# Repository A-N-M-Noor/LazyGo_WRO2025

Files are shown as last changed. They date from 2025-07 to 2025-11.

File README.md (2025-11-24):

<div align="center">
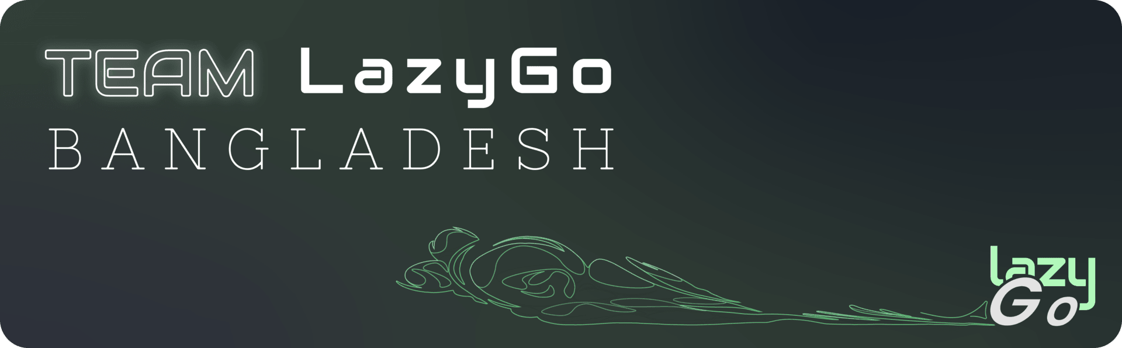
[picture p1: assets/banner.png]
  
</div>
  <strong>Team LazyGo</strong> is a robotics team from <strong>Bangladesh</strong>. Originally formed in 2022, LazyGo won <strong>3rd place</strong> at the Future Engineers category of the World Robot Olympiad International Round. Now the team returns again with three experienced international participants.
<br><br>

We named our robot **LazyBot**, which is built for the **Future Engineers** category in the **World Robot Olympiad 2025**. This year, we are trying to bring some interesting changes from the typical way a robot is built for this category. Definitely check out [Odometry Calculation](#odometry), [Disparity Extender Algorithm](#avoidance-using-lidar), and [LiDAR Based Tower Detection](#obstacle-round) algorithms.

This repository contains all the files, codes, models, photos and everything about our team and the robot.

Visit our team socials:





## Table of Contents

- [`Team Introduction`](#team-introduction)
- [`Mission Overview for WRO Future Engineers Rounds`](#mission-overview-for-wro-future-engineers-rounds)
- [`Repository`](#repository)
- [`Key Features`](#key-features)
- [`Components and Hardware`](#components-and-hardware)
- [`Algorithm`](#algorithm)
- [`Mobility Management`](#mobility-management)
- [`Power and Sense Management`](#power-and-sense-management)

---
## Team Introduction
<div>
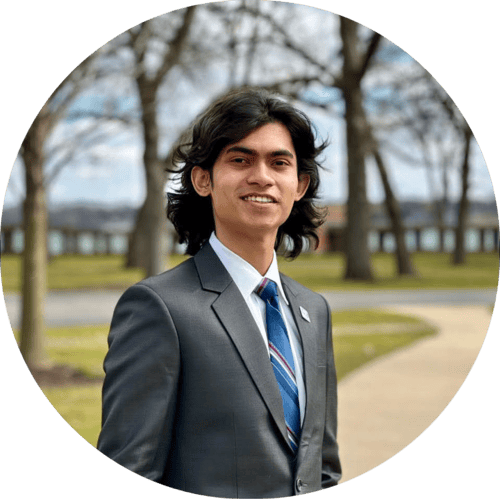
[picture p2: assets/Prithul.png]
  <br>
  <strong>Iqbal Samin Prithul</strong><br>
  Embedded Electronics<br>
  WRO 2022 International 3rd Place (Future Engineers Category)<br>
  <a href="mailto:prithul0218@gmail.com">prithul0218@gmail.com</a>
</div><br>

---
<div>
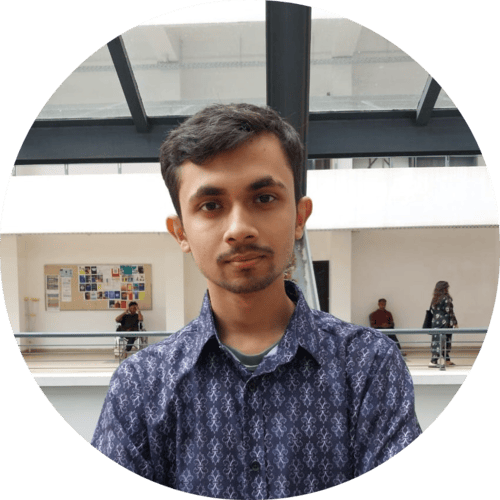
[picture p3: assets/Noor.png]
  <br>
  <div align="right">
  <strong>A.N.M Noor</strong><br>
  Software and ROS<br>
  WRO 2023 International Participant (Future Engineers Category)<br>
  <a href="mailto:noornoorrohan15@gmail.com">noornoorrohan15@gmail.com</a></div>
</div><br>

---
<div>
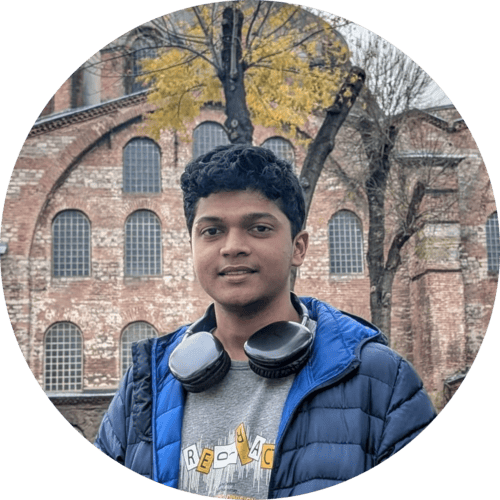
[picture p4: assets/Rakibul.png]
  <br>
  <strong>Rakibul Islam</strong><br>
  Hardware and CAD design<br>
  WRO 2024 International Participant (Future Engineers Category)<br>
  <a href="mailto:rakibul.rir06@gmail.com">rakibul.rir06@gmail.com</a>
</div><br>

---

---

## Mission Overview for WRO Future Engineers Rounds

<table>
  <tr>
    <td width="50%" valign="top" align="center"><h3>🏁 Round 1: Lap Completion</h3></td>
    <td width="50%" valign="top" align="center"><h3>🏆 Round 2: Lap Completion with Obstacle Avoidance and Parking</h3></td>
  </tr>
  <tr>
    <td width="50%" valign="top" align="left">
      <p>In <strong>Round 1</strong>, the robot must autonomously complete <strong>three laps</strong> on a pre-defined track. The goal of this round is for the bot to demonstrate stable navigation and precise lap tracking without any obstacle avoidance requirements.</p>
      <ul>
        <li><strong>Objective</strong>: Complete three laps on the track within the allotted time.</li>
        <li><strong>Key Tasks</strong>: Accurate path-following, speed control, and lap counting.</li>
      </ul>
      <div align="center" valign="bottom">
        <br><br><br><br>
        Round 1 WRO Track
      </div>
    </td>
    <td width="50%" valign="top" align="left">
      <p>In <strong>Round 2</strong>, the bot must complete <strong>three laps</strong> while avoiding green and red obstacles:</p>
      <ul>
        <li><strong>Green Obstacles</strong>: The bot should move <strong>left</strong> to avoid.</li>
        <li><strong>Red Obstacles</strong>: The bot should move <strong>right</strong> to avoid.</li>
      </ul>
      <p>After completing the laps, the bot must accurately park within a designated zone.</p>
      <ul>
        <li><strong>Objective</strong>: Complete three laps, avoid obstacles, and park in the designated area.</li>
        <li><strong>Tasks</strong>: Obstacle detection, color-based avoidance, and precision parking.</li>
      </ul>
      <div align="center">
        Round 2 WRO Track
      </div>
    </td>
  </tr>
</table>

---
>[!IMPORTANT]
>**Important: WRO Future Engineers Rulebook**
>* **Thorough Reading:** Ensure that you thoroughly read the **WRO Future Engineers 2025 Rulebook** to understand all rules and guidelines.
>* **Official Link:** Access the rulebook here: [🔗 WRO Future Engineers 2025 Rulebook](https://wro-association.org/wp-content/uploads/WRO-2025-Future-Engineers-Self-Driving-Cars-General-Rules.pdf).

---
## Repository

This repository includes all files, designs, and code for **LazyBot**, our WRO 2025 robot.

### File Structure

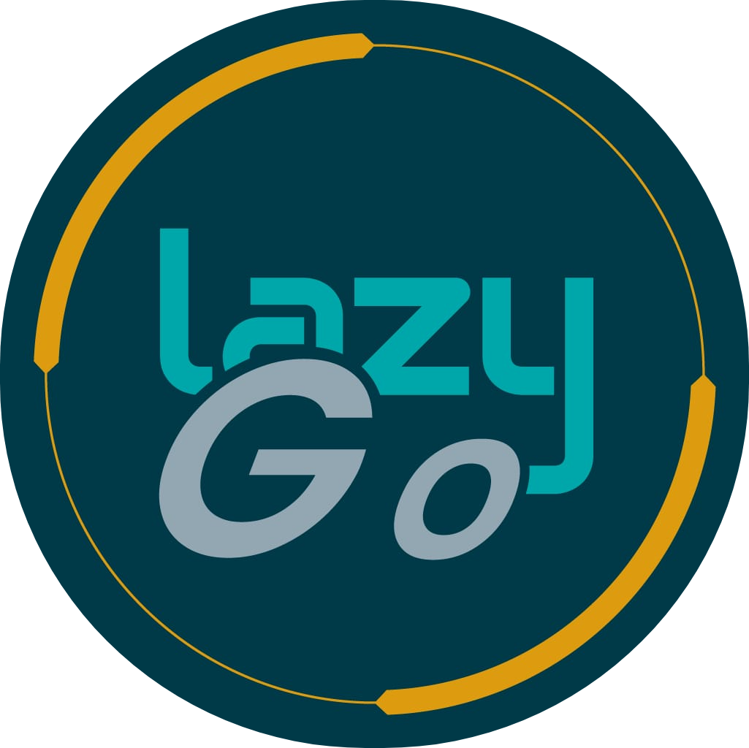
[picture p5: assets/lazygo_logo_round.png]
LazyBot

Here’s a breakdown of the project folders:

- **[`assets`](./assets/)**: Contains all the images used in the README files of this repository.
- **[`instructions`](./instructions/)**: Contains all the instructions on how to setup and use the package.
- **[`models`](./models/)**: Contains 3D models and CAD designs of the robot.
- **[`src`](./src/)**: Source code for the robot's programming. This contains the ROS2 packages.
- **[`t-photos`](./t-photos/)**: Technical images of the robot build.
- **[`v-photos`](./v-photos/)**: Visual photos for aesthetics and showcasing.
- **[`video`](./video/)**: Performance and demo videos of LazyBot.

---
---

## Key Features

- **`Hybrid LEGO & 3D Printed Design`**: Using LEGO parts proved to be very helpful based on the previous experience of our members. That, along with 3D printed parts made it possible to harness LEGO's precision and the flexibility of 3D printing.
- **`Advanced Sensor Suite`**: LazyBot is equipped with a LiDAR (to perfectly sense the surroundings), encoder motor (to precisely calculate the position), IMU (to calculate realtime orientation).
- **`Use of Robot Operating System`**: We used ROS2 to control the robot. We took this decision because Robot Operating System allows to make a project very modular and provide a lot of useful tools for simulation and visualization.
- **`Real-Time Odometry Calculation`**: This is one of the major feature of our robot. Using the onboard IMU sensor and the value from the motor's encoder, the robot calculates the exact realtime position of the robot.
- **`Efficient Debugging`**: We've added an OLED display to the MCU of the robot which helps to debug the issues on the MCU side. And ROS2 provides a lot of debugging tools that helps us debug any issues happening on the Pi side.

---
---

## Components and Hardware

Our bot is equipped with various components that support its autonomous functionality. The table below summarizes each module with a concise role and mounting approach:

<table>
  <thead>
    <tr>
      <th>Image</th>
      <th>Component</th>
      <th>Price</th>
      <th>Role / Function</th>
      <th>Mounting</th>
    </tr>
  </thead>
  <tbody>
    <tr>
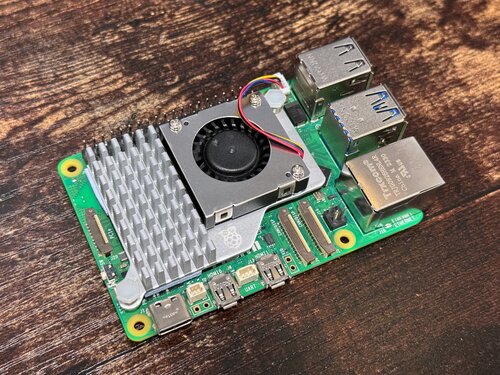
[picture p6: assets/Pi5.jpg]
Raspberry Pi 5
      <td></td>
      <td><a href="https://www.aliexpress.com/item/1005008153885728.html">Raspberry Pi 5</a></td>
      <td>$100.00</td>
      <td>High‑level processing (ROS2, vision, LiDAR integration). 8GB RAM for parallel tasks.</td>
      <td>3D printed middle chassis plate + 4× M2.5 standoffs & screws.</td>
    </tr>
    <tr>
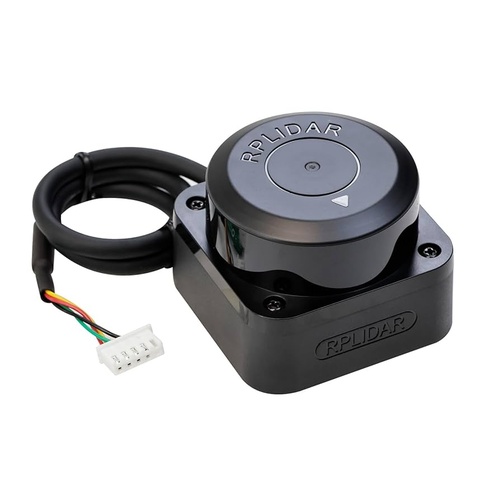
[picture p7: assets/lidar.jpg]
RPLidar C1
      <td></td>
      <td><a href="https://www.aliexpress.com/item/1005007915572042.html">RPLidar C1</a></td>
      <td>$67.87</td>
      <td>360° environment scan for obstacle mapping & tower shape profiling.</td>
      <td>Top cover LiDAR mount, 4× M2.5 screws. Resting on middle layer tray for support.</td>
    </tr>
    <tr>
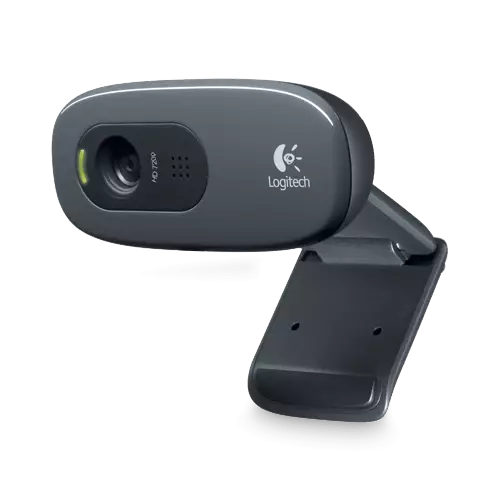
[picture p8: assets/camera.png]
C270
      <td></td>
      <td><a href="https://www.aliexpress.com/item/1005005033359539.html">Logitech C270 Camera</a></td>
      <td>$24.76</td>
      <td>Color tower detection (masking & confirmation).</td>
      <td>Mounted on 3D printed pan servo mount with single screws for angle adjustment.</td>
    </tr>
    <tr>
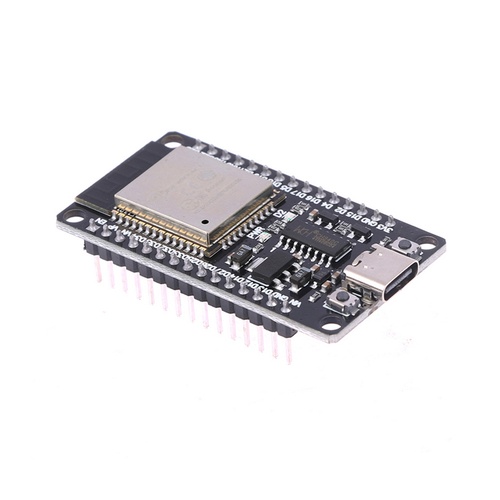
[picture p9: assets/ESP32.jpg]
ESP32
      <td></td>
      <td><a href="https://www.aliexpress.com/item/1005006826620736.html">ESP32 Microcontroller</a></td>
      <td>$7.38</td>
      <td>Real‑time motor, encoder, IMU, servo & OLED interface; low‑level comms.</td>
      <td>Soldered to custom secondary PCB under top cover.</td>
    </tr>
    <tr>
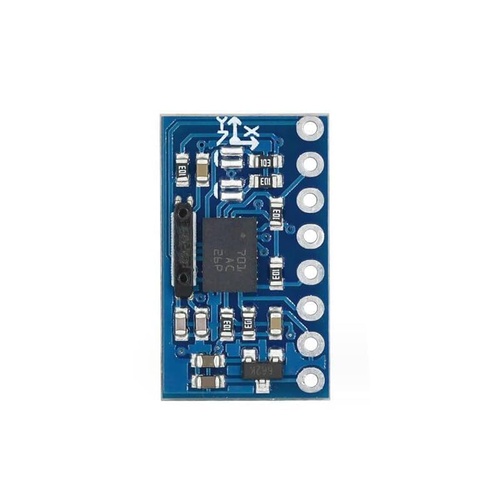
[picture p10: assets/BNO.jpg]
BNO055
      <td></td>
      <td><a href="https://www.aliexpress.com/item/1005009534591471.html">BNO055 9‑Axis IMU</a></td>
      <td>$22.28</td>
      <td>Orientation & fused heading for odometry; low drift angle source.</td>
      <td>Center (slightly left) of PCB for vibration isolation; header pins + foam tape as spacer for mild vibration dampening.</td>
    </tr>
    <tr>
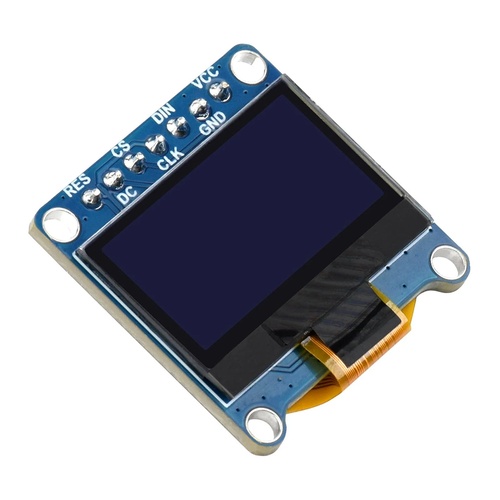
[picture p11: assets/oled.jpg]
OLED
      <td></td>
      <td><a href="https://www.aliexpress.com/item/1005008934254841.html">1.3" OLED (I2C)</a></td>
      <td>$5.83</td>
      <td>Live status: sensor readouts, battery warnings, debug info.</td>
      <td>Vertical raised header on PCB rear edge + friction with top cover.</td>
    </tr>
    <tr>
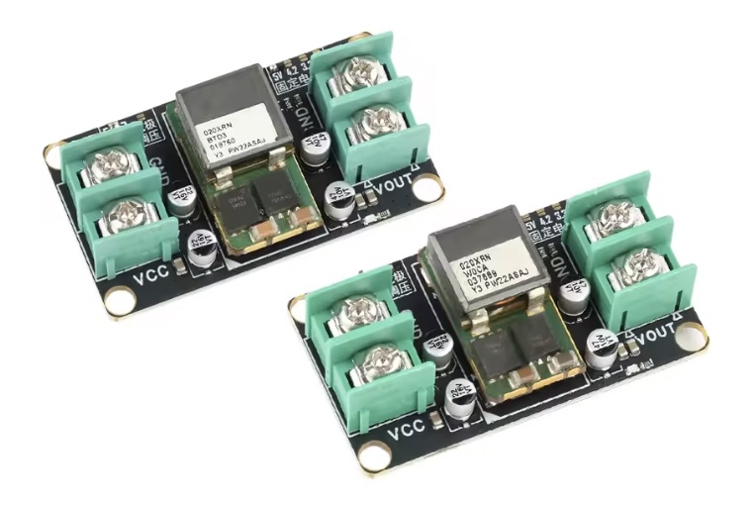
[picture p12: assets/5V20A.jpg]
5V 20A Buck
      <td></td>
      <td><a href="https://www.aliexpress.com/item/1005008785628197.html">5V 20A Buck Converter</a></td>
      <td>$6.21</td>
      <td>Primary regulated 5V rail for Pi (headroom for peaks).</td>
      <td>Middle chassis plate with double sided tape.</td>
    </tr>
    <tr>
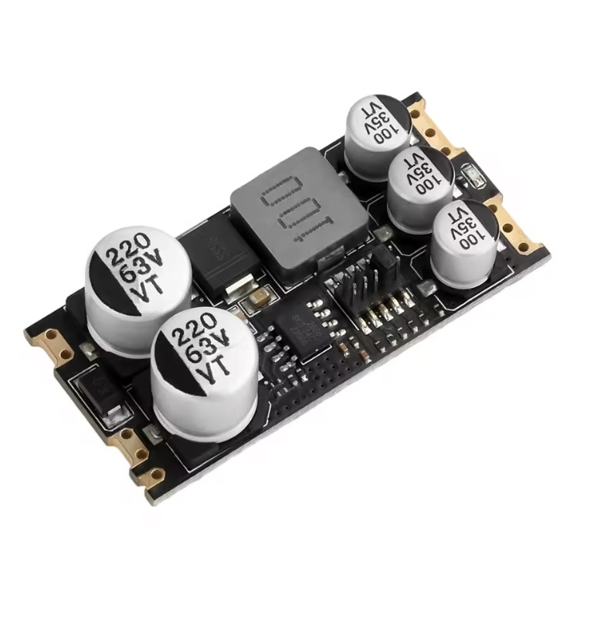
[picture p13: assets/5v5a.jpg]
5V 5A Buck
      <td></td>
      <td><a href="https://www.aliexpress.com/item/1005008477697348.html">5V 5A Buck (SCT2650)</a></td>
      <td>$3.99</td>
      <td>Secondary regulated supply for noise generating components (Servo, peripherals).</td>
      <td>Bottom of PCB (to save space).</td>
    </tr>
    <tr>
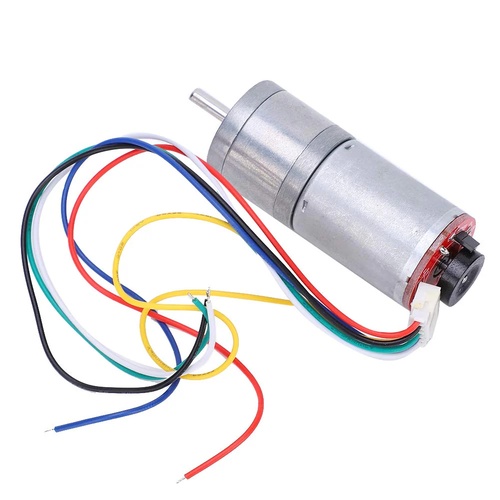
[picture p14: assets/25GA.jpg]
25GA Motor
      <td></td>
      <td><a href="https://www.aliexpress.com/item/1005008766288833.html">25GA Gear Motors + Encoder</a></td>
      <td>$9.65</td>
      <td>Drivetrain torque + linear displacement feedback for odometry.</td>
      <td>Captured in printed motor housings; 2× M3 screws.</td>
    </tr>
    <tr>
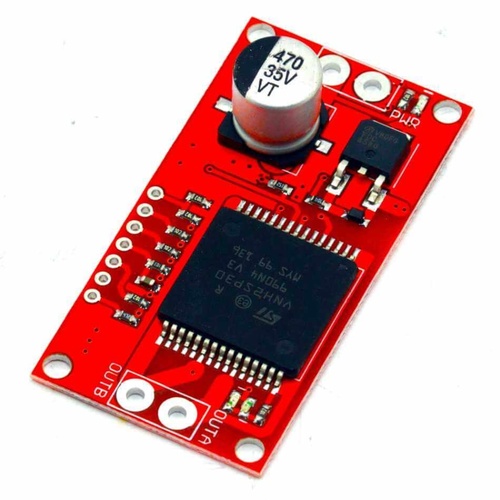
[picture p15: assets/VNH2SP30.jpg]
Motor Driver
      <td></td>
      <td><a href="https://www.aliexpress.com/item/1005006213746966.html">VNH2SP30 Motor Driver</a></td>
      <td>$18</td>
      <td>High‑current brushed DC control (PWM + direction + protection).</td>
      <td>Screwed to the bottom of the second/middle layer.</td>
    </tr>
    <tr>
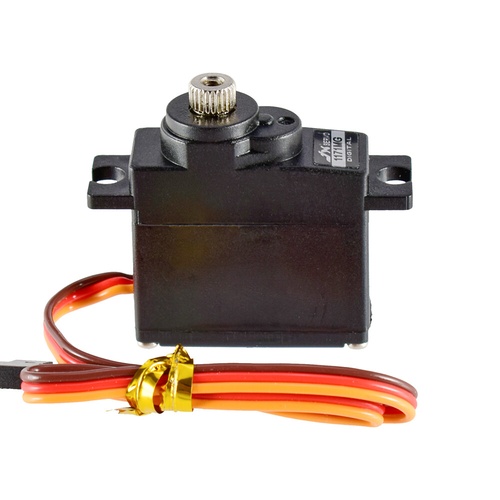
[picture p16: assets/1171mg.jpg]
Servo
      <td></td>
      <td><a href="https://www.aliexpress.com/item/1005002533411942.html">PS1171MG Servo</a></td>
      <td>$16.00</td>
      <td>Steering actuation & camera pan positioning.</td>
      <td>3D printed steering bracket/3D printed LiDAR bracket with integrated servo hole. 2× self‑tapping screws each.</td>
    </tr>
    <tr>
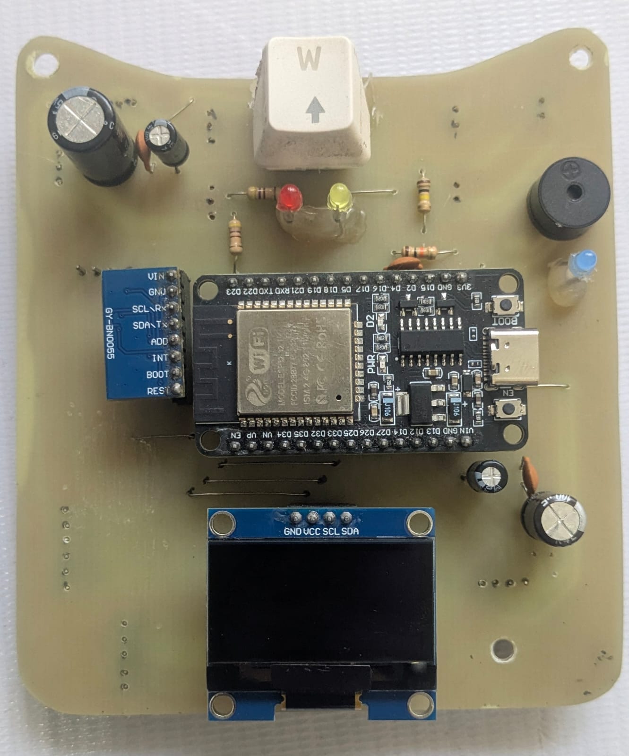
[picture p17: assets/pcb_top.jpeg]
Secondary PCB
      <td></td>
      <td>Custom Secondary PCB</td>
      <td>N/A</td>
      <td>Integration hub: ESP32, IMU, OLED, some power distribution, headers and lots of capacitors.</td>
      <td>Four M3 standoffs to chassis mid‑deck and top cover.</td>
    </tr>
    <tr>
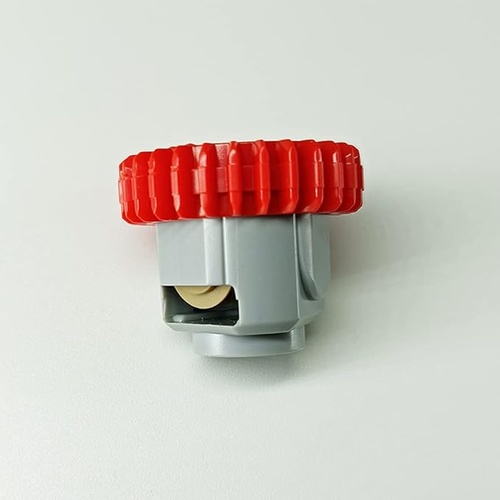
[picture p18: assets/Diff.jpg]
Differential
      <td></td>
      <td><a href="https://www.aliexpress.com/item/1005007345491844.html">LEGO Differential (Gen 3)</a></td>
      <td>$1.84</td>
      <td>Allows inner/outer wheel speed difference for smooth turning.</td>
      <td>Seated in printed cradle; retained by axle bearings (friction).</td>
    </tr>
    <tr>
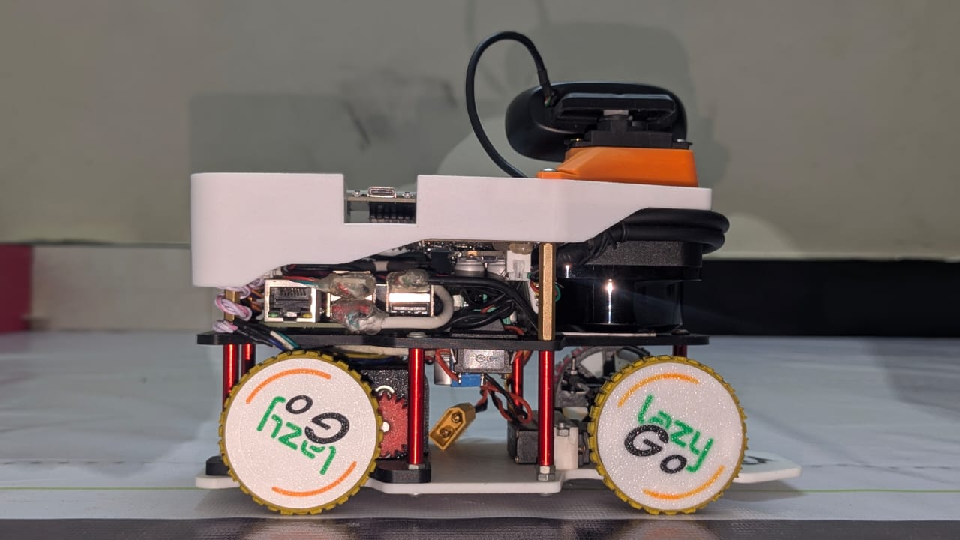
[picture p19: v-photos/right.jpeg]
Frame
      <td></td>
      <td>3D Printed Body Frame</td>
      <td>Varies</td>
      <td>Structural chassis: mounting surfaces, protective shell. 3 Layer design.</td>
      <td>Base structure (printed as modules with minimum support); screw or snap‑fit/friction.</td>
    </tr>
  </tbody>
</table>

> More details on the Power and sensing components can be found below.
---

## Algorithm and Software
ROS2 underpins our control system, letting us split functionality into modular nodes. Real‑time odometry (encoder + IMU) drives lap counting and parking logic. Tower detection combines LiDAR shape cues with camera color checks. Gazebo simulation allowed rapid iteration before deploying to hardware.
> [**More details on software is in the `/src` directory.**](/src/)

## **Mobility Management**

This segment outlines the mobility system of **LazyBot**, with two key features: a differential gear system, and Ackermann steering. But first, a little bit about our chassis design and motors:
### The Chassis Design
The LazyBot chassis was designed completely from scratch on OnShape 3D for online collaboration and ease of use on lower end computers. The robot has 3 separate layers, which are held together using M3 metal standoffs.
1. **First/Bottom layer:** 
     - 5mm above ground.
     - 3mm thick 3D-printed sheet with mounting holes.
     - Holds steering mechanism + servo motor, LiPo Battery, main differential drive +25GA motor.
2. **Second/Middle Layer:**
   - 36mm above the bottom layer.
   - 3mm thick 3D-printed sheet with mounting holes.
   - Holds Raspberry Pi 5, 5V 20A buck converter, VNH2SP30 motor driver.
   - Supports LiDAR from the bottom.
3. **PCB and top cover:**
   - 30mm above the second layer.
   - Acts as the third layer, with a light 3D printed top cover 15mm offset from the top of the PCB.
   - The top cover also mounts the LiDAR and camera pan servo.

#### **Step-by-step assembly:**
Assembly of the robot is simple as it is built from the bottom up. The first layer can be assembled first with all the components it holds and the wheels installed. Adding the standoff to the bottom layer - we can continue to the second layer, which should be partly pre-assembled with the motor driver at the bottom and the buck converter + Raspberry Pi 5 mounted at the top. At this point, partial wiring can be done between the first and second layer. Then, the PCB is assembled at the top with 30mm standoffs. Upon connecting all the cables to the PCBs using JST connectors, the top cover is mounted with preinstalled LiDAR. The camera pan servo should be pre-inserted into the top cover with its dedicated wire routing slot. Then, everything can be closed off with appropriate wiring through the wiring holes/slots. We recommend checking out our complete 3D model if you get stuck at any step.

### The 25GA370 Motor

DC motors provide the best balance between performance, complexity and budget for the main drive train. So we initially wanted to use a 20GA motor for its torque, speed, and size being just right from our experience. However, after our first 20GA sized motor from China refused to stop working, we had to resort to the more commonly and locally available 25GA motor. 

The motor provides sufficient torque at slow speeds with decent maximum speeds. The encoder, with its roughly 1870 ticks per meter precision, does a great job at measuring robot precision at millimeter level accuracy.

### Servo Selection:
Since we are using two servos in our system, we decided to use the same servo for both mechanism to allow for less individual part count. The PS-1171mg was an excellent choice, available in the Bangladeshi local market. Its metal gears give us peace of mind, and 0.13sec/60° movement speed was adequate for our robot.

### Differential Drive System

Our robot utilizes a **3rd generation LEGO differential gearbox**. Differential drive is a crucial feature for smooth cornering and precise movements. The Lego Gearbox is small with low backlash, something we were not able to achieve with gears printed on our 3D printer.

<table>
<tr>
<td width="50%">

#### How It Works:
- The motor is connected to the differential gearset using a matching 20 teeth 3D printed gear. The gear system transfers torque from the motor to the gearbox with a **1:1.2** ratio.
- The differential automatically compensates for wheel speed differences when turning.
- Encoder readings stay accurate as it records roughly the average speed of the two wheels.

#### Benefits of our drive train:
1. **Smooth Turning**: Independent wheel speeds allow efficient navigation.
2. **Precise Odometry**: Encoders enhance path planning and tracking.
3. **Compact & Modular**: LEGO-based integration makes the drivetrain easy to modify and assemble.
4. **Freedom to change gear ratio**: 3D printing one gear allowed us to change the gear ratio, as our motor was just a tad bit too fast.

<div align="center">
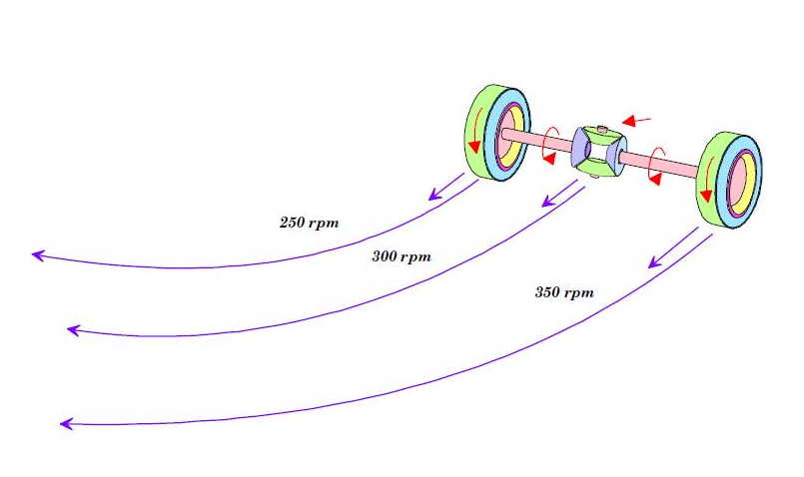
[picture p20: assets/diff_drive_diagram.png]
Differential Gear Diagram
  
</div>

</td>
<td width="50%">
<div align="center">
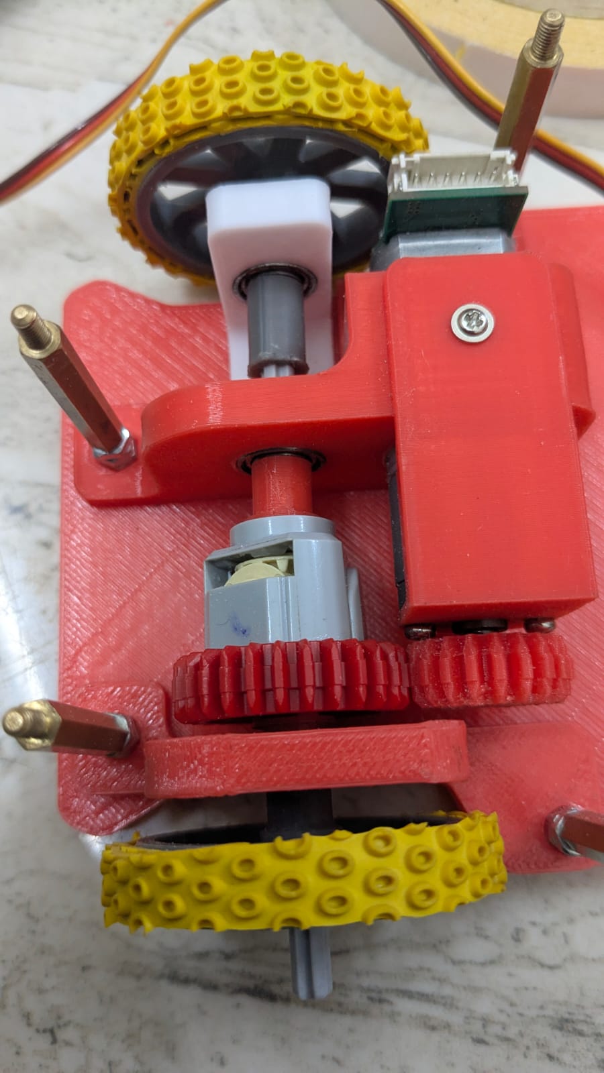
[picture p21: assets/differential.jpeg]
Differential Drive Setup
  
  <br>
  A 20GA Motor was being used when we took this picture.
</div>
</td>
</tr>
</table>

### **Steering System - 3D Printed Ackermann Mechanism**

The robot features a **3D printed Ackermann steering system** controlled by a **servo motor**. This configuration allows the front wheels to turn at appropriate angles during a corner, minimizing tire slippage and improving steering accuracy.

##### Advantages:
1. **Sharper turns**: While not important in such small scale, the mechanical efficiency that comes with the Ackermann design allows sharper turns.
2. **Customizable Design**: 3D printed components allowed fine-tuning and easy iteration.
3. **Precise Control**: Servo-driven mechanism ensures consistent and accurate angle adjustments.
4. **Adjustable links**: We used off-the-shelf RC car links to connect the servo to the steering knuckles.

<div align="center">
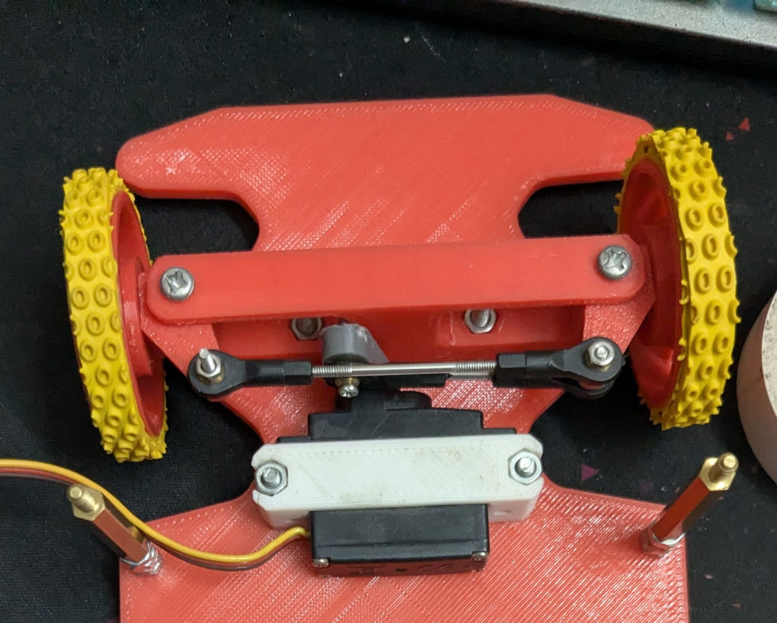
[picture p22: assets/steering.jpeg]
3D Printed Ackermann Steering System
  
</div>

---
---

## Power and Sense Management

Our robot has been designed to optimize performance while ensuring reliable power delivery, precise sensing, and efficient communication between components.

It is powered by a 3-cell lithium battery. Two dedicated buck converters for high and low noise devices. This structure ensures stable operation across core modules like the Raspberry Pi 5, RPLidar, ESP32, sensors, and motor systems. The decision to use separate buck converters was made when we found out that the servo motors can take a significant amount of in-rush current, which was causing our Raspberry Pi to throttle, and ESP32 to go into brownout detection causing a reset.

Below is the complete schematic of the PCB. External to the PCB, we have the 5V 20A buck converter, and a DC motor driver.

---
<div align="center">
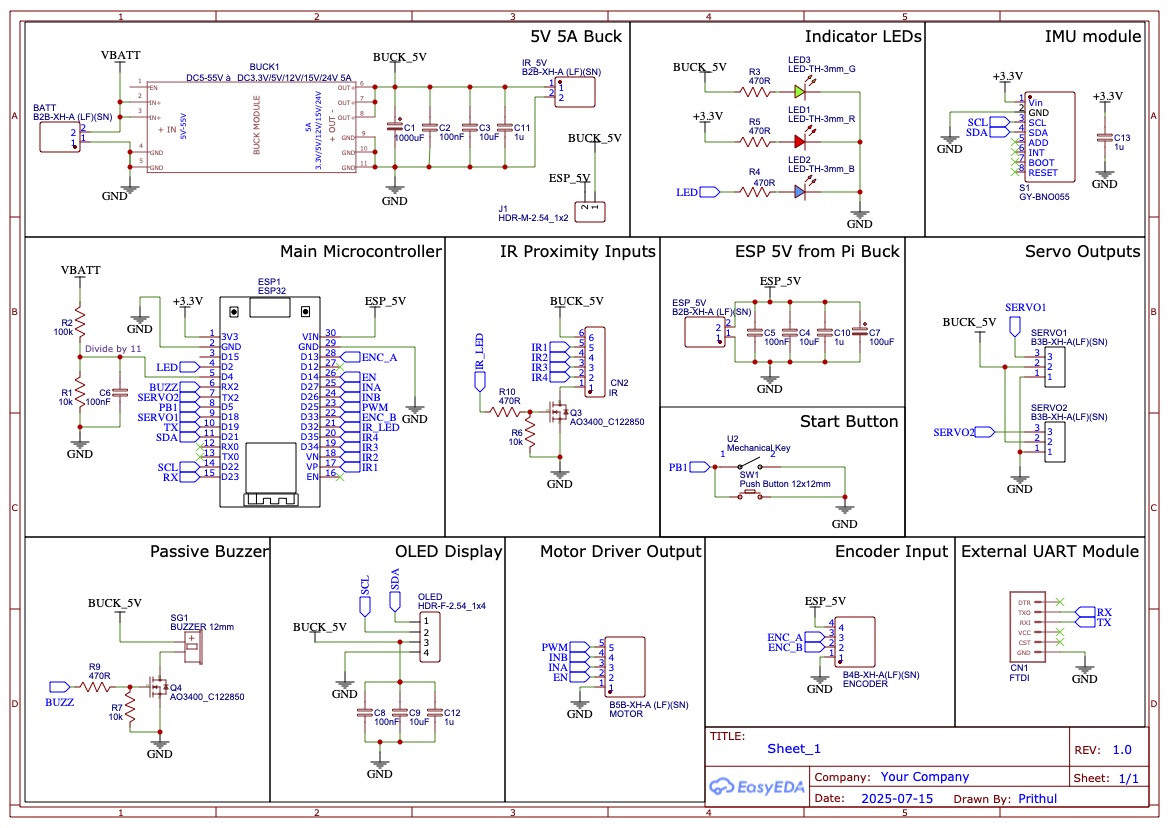
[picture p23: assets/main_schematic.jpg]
Main Schematic of the PCB
  
</div>

### Here is a detailed explanation of the power and sense components:

#### **1. Power Source: 3-Cell Lithium Polymer Battery**
- **Configuration**: 3S (3 cells in series)
- **Voltage**: 12.6V (fully charged) → ~11.1V (nominal) → ~9.9V (discharged)
- **Benefits**:
  - High energy density
  - Sufficient current delivery for high-load components like Motors, Pi and LiDAR
  - Rechargeable and easily sourceable

---

#### **2. Main 5V 20A Buck Converter (Unknown chip)**
- **Purpose**: Supplies 5.1V to **Raspberry Pi 5, RPLidar C1, and ESP32**
- **Input**: Directly from the 3S battery (~12.6V max)
- **Output**: Stable 5.1V 
- **Benefits**:
  - Ensures separate 5V with separate ground path so that the servo current does not affect other modules. 
  - Enhances RPLidar C1 and Encoder precision with reduced noise.

---

#### **3. Secondary 5V 5A Buck Converter (SCT2650)**
- **Purpose**: Supplies 5V to **Servo, OLED, Buzzer**
- **Input**: Directly from the 3S battery (~12.6V max)
- **Output**: Rush currents at 5V / 5A
- **Benefits and reason to choose**:
  - The SCT2650 is a near-identical copy of the Texas Instruments TPS54560 chip, efficient design.
  - Chosen for it's excellent noise free design with multiple capacitors in series, and high current Schottky diode.
  - There is no overcurrent protection false-triggering when the servos draw sudden in-rush current. This is an issue we had before with the Mini 560 Buck converter.

---

#### **4. VNH2SP30 Motor Driver with Built-in Regulator**
- **Purpose**: Drives the **25GA motor**
- **Regulation**: Built-in buck handles motor voltage directly from the 3S battery
- **Features**:
  - No external 5V needed
  - Simplifies wiring and improves efficiency
  - Has very low RDS(on) resistance with integrated protections
  - Something we had easy access to in the market :)

---

### Voltage Distribution Table

| Component | Voltage Supplied | Power Source / Converter |
|---|---|---|
| **Raspberry Pi 5** | 5.1V* | Unknown chip 5A Buck |
| **RPLidar C1** | 5.1V* | Unknown chip 5A Buck |
| **ESP32 + Sensors** | 5.1V* | Unknown chip 5A Buck |
| **Servo Motor + OLED** | 5V | SCT2650 5A Buck |
| **Motors (25GA with encoder)**| Battery Voltage  | VNH2SP30 Motor Driver (built-in) |

> ***The 5V 20A buck converter module has a 2.8V-5.6V adjustable potentiometer, which allows us to conveniently set the voltage to 5.1V. This helps avoid throttling on the pi caused by voltage drop on the wire and PCB.**
#### Flowchart for ease of understanding:
<div align="center">
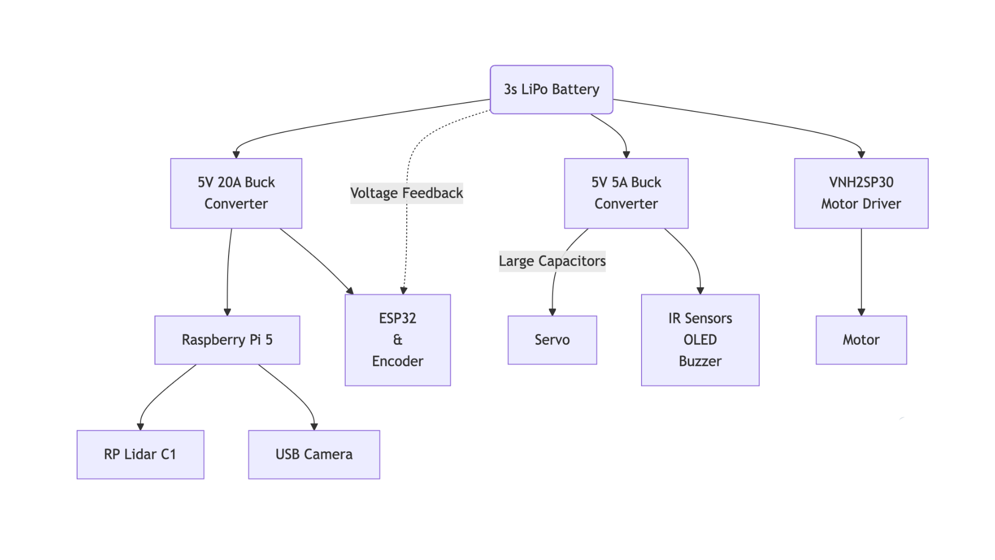
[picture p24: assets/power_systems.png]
  
</div>

---
---

## Custom Homemade PCB
Since SMD PCB manufacturing is not available to public in Bangladesh, and services like JLCPCB are extremely expensive due to unfair customs taxes, we had to design our own through hole PCB and manufacture it right at home.

The PCB is designed to use locally available components, with a lot of board clearance to allow us to etch the PCB using ferric chloride. The process included:
1. Printing a mirrored black and white version of the copper traces on a glossy paper.
2. Transferring the ink onto the PCB using an iron on the PCB with the glossy paper sandwiched in between.
3. Fixing minor transfer errors with a permanent black marker.
4. Etching the PCB in a ferric chloride solutions for a fixed amount of time (gained through experience).
5. Cleaning up the board with isopropyl alcohol and mildly sanding the copper to clear oxidization.
6. Applying a thin layer of resin to coat the copper traces.

### PCB Views

| **Top View of the PCB** | **Bottom View of the PCB** |
|---|---|
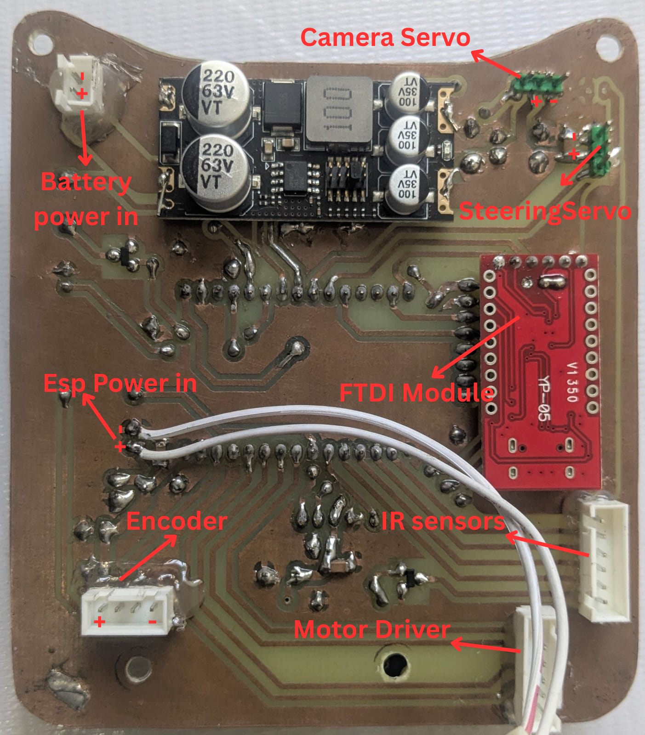
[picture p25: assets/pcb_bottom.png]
|  |  |

---
---

Thank you for going through our documentation! If you want to learn more, please reach out to us through our socials media accounts:

- [facebook](https://www.facebook.com/team.lazygo)
- [linkedin](https://www.linkedin.com/company/lazygo)

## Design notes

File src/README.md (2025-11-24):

# Codebase of LazyBot
This directory contains all the code of LazyBot (By Team LazyGo)

File structure:
```
src
├── ESP32 Code                          (PlatformIO Project for the ESP32)
│   └── src/                            (Contains the C++ code for ESP32)
|
├── lazy_interface/                     (ROS Package - Message Types)
│   ├── msg/                            (Contains custom message types used by ROS to control the robot)
│   └── srv/                            (Currently, we're not using any custom ROS services)
|
├── lazybot/                            (ROS Package - Control Package)
│   ├── launch/                         (Contains launch files to launch necessary nodes together)
|   |   ├── open.lazy_launch.py         (Launch file for open challenge)
|   |   ├── robot.lazy_launch.py        (Launch file for obstacle challenge)
│   |   └── sim.lazy_launch.py          (Launch file for simulation run)
|   └── lazybot/                        (ROS Nodes - contains all the code files for control package)
|
└── lazysim/                            (ROS Package - Gazebo Simulation)
    ├── config/                         (Configure files for the simulation)
    |   └── track.yaml                  (Configure the simulated track)
    └── launch/                         (Contains launch files to launch necessary nodes together)
        ├── control.launch.py           (ROS-Control package launcher: This is needed to control the robot in simulation world)
        ├── gazebo.lazyBot.launch.py    (Launches the simulation world with robot model)
        ├── lazySim.launch.py           (Only launches the robot model.)
        └── rviz_lazySim.launch.py      (Launches RVIZ with appropriate topics and settings)
```

# Software Decisions

This time, software-wise, we focused on a few specific aspects of the robot. Even though each member worked in different areas, we all had some goals in mind. For the software part, we wanted to make sure of the following things:
- **Reliability:** The robot should be very reliable. It cannot behave randomly at different times. Even if the robot doesn't work the issues should be reproducible. Hence, we decided to use ROS2 because it enabled us to test individual parts of the robot and merge them into a robust piece of software. More on this [later...](#why-ros2)
- **Accurate Range Sensor:** The distance calculations must be accurate and reliable in order for the software to meet our requirements. We need something more reliable than ultrasonic distance sensors. Therefore, we decided upon using a LiDAR. We chose RPLidar C1 because, well, it was the cheapest option! But considering the price, it performs really well. The output point cloud is very clean and noise-free. The only issue is that the scan rate is only 10Hz. But overall we believe it was a good decision. ROS2 was useful here as well as RPLidar has an existing ROS Package to use their LiDARs. So maybe a LiDAR with a higher scan rate would be better if it gives a similar quality output.
- **Odometry:** We wanted to have accurate odometry calculation for the robot's movement. This was done using a fusion of IMU sensor values and motor encoder values. The detailed [algorithm](#odometry) is explained below.
- **ESP32 as a 2nd Brain:** We cannot directly control the actuators from the Raspberry Pi. A regular microcontroller gives far more control over its GPIO pins than a Pi does. Currently, we are extensively using the ESP32 microcontroller's FreeRTOS feature to manage different tasks like keeping serial communication, reading sensor data, showing debug info on an OLED display, etc. Even though we initially wanted to use an ESP32 only for controlling the motors and getting sensor data, we later offloaded a few logic elements to the ESP as well. The tasks that require instant reaction - mainly the parking tasks - are handled mostly by the ESP32.
- **Object Detection Issues:** From previous experience, we know that detection of the towers can sometimes be very tricky. Because we found the objects given during the international round to be very dark for the camera to properly detect them, we spent a lot of time thinking about a possible solution for this. In the end, we decided to use a lower FOV camera with a servo to directly look at a target object and detect its color. The [algorithm](#obstacle-round) for this is explained in detail below.
- **Gazebo Simulation:** Due to academic reasons, the main programmer of our team, Noor, had to stay away from the team for a residential semester. During that time, he did not have access to the physical robot, which made it very difficult for him to program the logic for the robot. So he set up a Gazebo simulation environment and perfected the robot's logic there. When he finally had access to the robot, he implemented the code on the physical robot. ROS2 was very useful here as well. As Gazebo is compatible with ROS2, the same code used for the simulation could also be used for the robot as well. More on that [later...](#gazebo-simulation-and-its-role-in-our-development-workflow)

### Why ROS2
ROS2 (Robot Operating System 2) is a flexible, open-source framework for writing robot software. It provides a collection of tools, libraries, and conventions that simplify the complex task of creating robust and scalable robotic systems. 

In ROS2, different programs simultaneously run as independent nodes that communicate via various middleware interfaces. Many off-the-shelf components also have dedicated ROS2 packages that make it simple and easy to use them. ROS2 also comes with a number of debugging tools like rqt-graph, topic echo, rviz, etc. ROS2 sends its messages over the local network, which makes it possible to debug a robot from a different device just by connecting them to the same network. Currently, our robot mainly has three types of nodes running: one for serial communication with the ESP32, one for using the camera for object detection, and one for deciding how the robot should move. To give an example, we separated the logic for regular control and parking control into two different nodes. Even though they share information with each other, they can also work independently. So even if we make a few changes to one of them, the other one isn't affected. It also means we can run only the parking node and test the parking portion without doing the whole run over and over again.

As mentioned before, ROS uses a node-based approach where multiple nodes each solve one specific task. But they also share information (e.g., sensor data, odom data, specific commands, etc). This information is called "messages," and it is shared through topics. Multiple nodes can share information on a topic and multiple nodes can subscribe to it as well. ROS2 provides a utility called `rqt_graph` which shows a graph of all the running nodes and the topics.

<table>
    <tr>
        <td align="center">
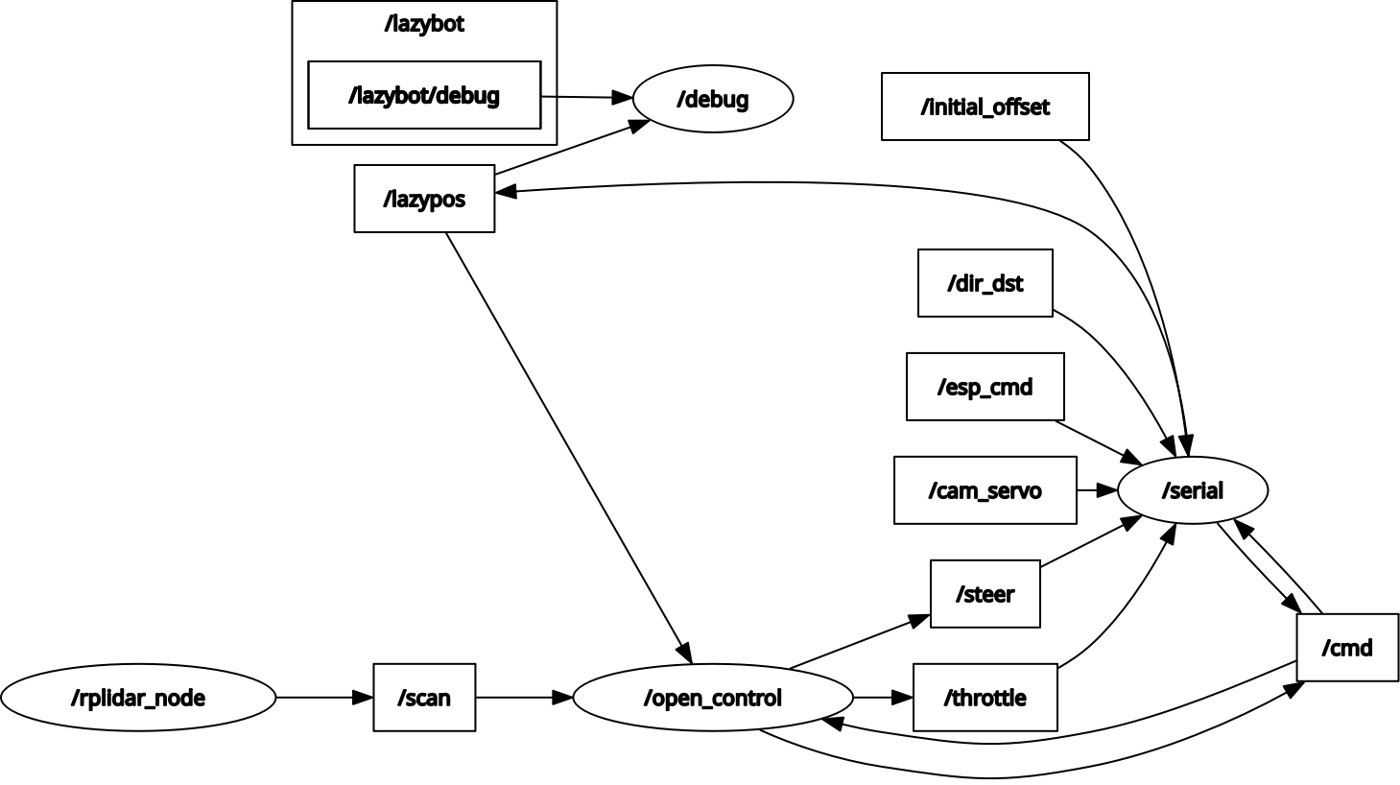
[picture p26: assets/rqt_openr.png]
RQT During Open Challenge
            
        </td>
        <td align="center">
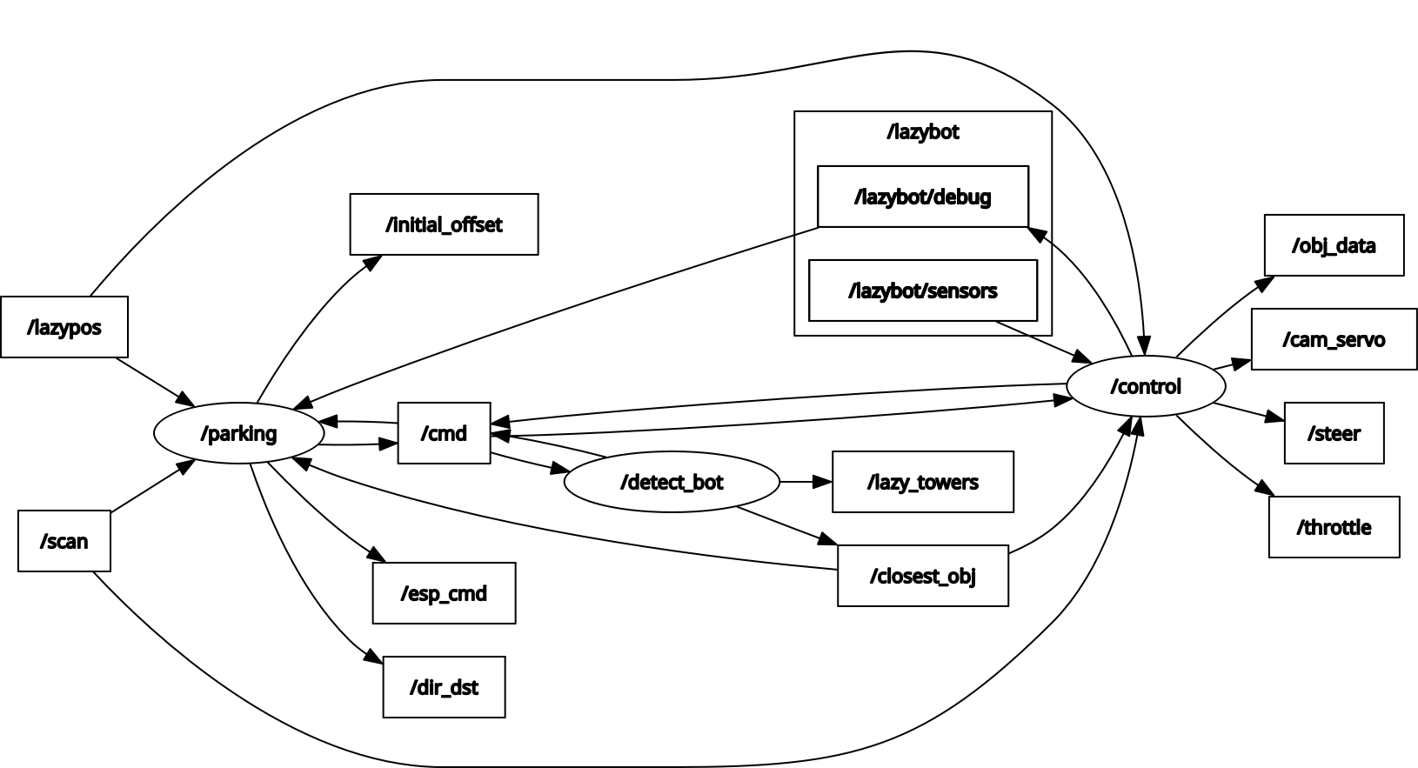
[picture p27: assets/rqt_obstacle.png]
RQT During Obstacle Challenge
            
        </td>
    </tr>
    <tr>
        <td align="center"><sub>This is the state of ROS2 when open challenge is running</sub></td>
        <td align="center"><sub>This is the state of ROS2 when obstacle challenge is running</sub></td>
    </tr>
</table>

### Serial Communication
We are typically used to sending `String` values from a computer to MCU and parse those strings to get the numerical values on the ESP side. Although parsing a number from a string value is not a big deal for a computer, or even for a Raspberry Pi, this is often unreliable and inefficient for an MCU because string parsing is a slow process and the data might get corrupted pretty easily due to parsing errors. 

So, we decided to use a **Hybrid Protocol**:
1. **ESP32 $\to$ Pi (RX):** Uses **Strings**. The ESP32 sends data like `[x,y,theta]` or status messages like `Start`, `Done`. Since the Pi has plenty of processing power, it can easily parse these strings. This also makes debugging easier as we can simply read the serial monitor to see what the ESP is saying.
2. **Pi $\to$ ESP32 (TX):** Uses **Raw Bytes**. To make the ESP32's job as easy as possible, the Pi sends commands as a sequence of 2 bytes: `[Key, Value]`. This requires zero string parsing on the ESP32 side—it just reads the bytes and executes the corresponding `case` in a switch statement.

#### Byte Protocol Encoding
Since we can only send integers between 0-255 in a single byte, we use a mapping system to send floating point values using bytes. 0 to 49 sets a key, and a byte of 50 to 250 means the value of that key. When ESP receives a byte between 0 to 49, it saves that key and waits for the value to arrive.

Here are a few examples:  
| Command | Key | Offset | Range |
| :--- | :--- | :--- | :--- |
| **Throttle** | 15 | 150 | -1.0 to 1.0 $\to$ 50 to 250 |
| **Steering** | 16 | 150 | -1.0 to 1.0 $\to$ 50 to 250 |
| **Camera Servo** | 17 | 140 | -90° to 90° $\to$ 140 to 230 |
| **Move Dist** | 7 | 150 | -1m to 1m $\to$ 50 to 250 |

This ensures that the ESP32 receives clean, error-free commands at a reasonable frequency.

#### Possible Improvement
As of now, only one byte is allocated for the value itself. This might not be enough on some occasions. For example, when we tried to send distance values from the LiDAR to the ESP32, we had to cap the distance value at 200cm, and lose sub-cm precision as well. Somehow allocating two or four bytes for the values should be a big improvement for this. Also, there are dedicated communication protocols which could have been used... For example, recently we explored MAVLink protocol. This is a really robust communication system used by high-end flight controllers like Pixhawk. But we didn't have enough time to implement it on our robot. Although it would have been an overkill for our robot anyways!

### Odometry
A really interesting feature of our robot is that it can calculate its realtime position. We achieved this by fusing the realtime orientation value with the motor's encoder values. When the robot is moving in a straight line, it is possible to calculate how far the robot has moved using the encoder values. But it is not so simple when the robot turns while moving. So when the robot is turning, we can actually divide its curved path into tiny sections that resembles straight lines. Then accumulating those straight lines and taking their directions into account, we can find the actual cartesian displacement of the robot with reliable precision.

Here's how it is calculated:
1. Find the delta of the encoder's value. Let's call it `ds`
1. Find the average angle between the last calculation and current heading angle. Let's call it `A`.
1. The movement vector would be: _(x = `ds*cos(A)`, y = `ds*sin(A)`)_
1. By accumulating this movement vector, we can find the realtime position of the robot.

Before getting a usable value, we had to calibrate our encoder to calculate values in metric units.

```mermaid
flowchart LR
    n1 --> D["Calculate delta encoder value: ds<br><br>Read current orientation angle<br><br>Find average angle (A) between last and current heading"]
    D --> E["Compute movement vector: x = ds * cos(A), y = ds * sin(A)"]
    E --> F["Accumulate movement vector to update position<br><br>Output realtime position"]
    A["Start"] --> n1
    F --> n1["Small Circle"]

    n1@{ shape: sm-circ}
```

### Open Round

#### Avoidance using LiDAR
During the open round, there are no towers on the track. So we don't need the camera. To move the robot in the track, we use a modified version of `Disparity Extender` algorithm. Here's a step by step description of the idea:

1. The LiDAR scans the area and gives a bunch of distances in many directions (one distance per ray).
1. For each ray, start with the ray’s measured distance as the “candidate” distance.
1. Look at the nearby rays around that ray. If any nearby ray’s obstacle is close enough that the car’s body would hit it when moving along the candidate ray, shorten the candidate distance to that nearby obstacle. (In other words: pretend the car is wide and see where it would first hit something.)
1. After doing that for every ray, you have a “safe distance” for every direction  -  the farthest you can travel in that direction without your body hitting something.
1. Pick the direction with the largest safe distance and steer the car toward it.

```mermaid
flowchart LR
    A["Start control loop"] --> B["LiDAR scan"]
    B --> C["Iterate"]
    C --> D["Set candidate distance from measured ray<br><br>Check nearby rays for potential body collision"]
    D --> F{"Nearby ray would cause collision"}
    F -- Yes --> G["Shorten candidate distance to nearby obstacle"]
    F -- No --> I["Save safe distance for current ray"]
    G --> I
    I --> J{"End of iteration?"}
    J -- No --> C
    J -- Yes --> L["Pick direction with largest safe distance<br><br>Steer car toward chosen direction"]
    L --> M["Repeat"]
    M --> B
```

One drawback of this method is that on straight sections, the robot shows a tendency to point itself toward the next corner. This happens because corners often look like the direction with the most open space before discovering the next turn, so the algorithm treats them as the safest option - even though the robot should ideally stay centered on the straight path. But this algorithm works really well to move between tight gaps. So the little drawback doesn't really matter to us. And of course, there are ways to improve on this issue.

One important thing to remember, the robot does not target the farthest distance, it targets the farthest `safe` distance - where it can move to without collision. Here's how it works:

<table>
    <tr>
        <td align="center">
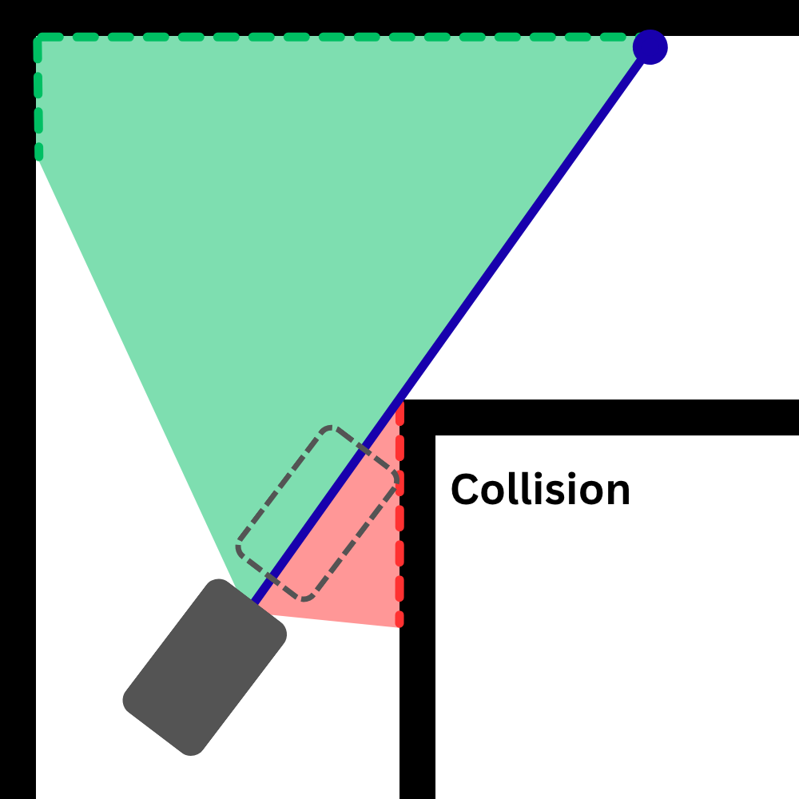
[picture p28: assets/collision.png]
Targetting farthest distance
            
        </td>
        <td align="center">
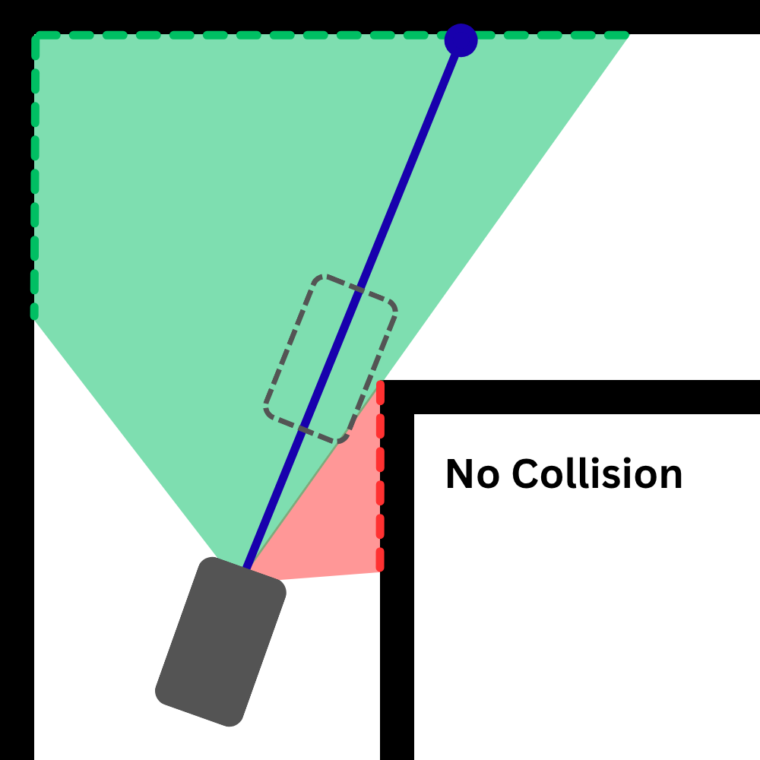
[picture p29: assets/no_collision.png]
Targetting farthest safe distance
            
        </td>
    </tr>
    <tr>
        <td align="center"><sub>Targeting farthest distance</sub></td>
            <td align="center"><sub>Targeting farthest `safe` distance</sub></td>
    </tr>
</table>

#### Lap Count
Because we can precisely calculate odometry, keeping lap count is a very simple task. The robot just keeps track of how many times it passes through the starting section. When it reaches the desired lap count, it just stops there. And it worked really well. The robot always stops between a few centimeters from the dead center of the starting section.

### Obstacle Round
It works similarly to the open round. But the robot needs to detect the towers. In our robot, tower detection is done in two ways.

1. `Using the camera`: This is a very basic color detection algorithm. From the camera feed, the robot detects the towers by masking colors.
1. `Using LiDAR data`: This approach is a bit more interesting. Towers create sudden changes (valley) in the LiDAR distance readings. If the readings suddenly get closer and then farther again, that usually means there’s an object in between. By checking how wide this change looks from the LiDAR’s point of view, we can estimate whether it matches the expected size of a tower. The object's size can be easily calculated using the formula `s = rθ`. If the size is around 5cm (width of a tower) the robot marks it as a possible tower. But it still confirms the color with the camera to be sure.

Here's how it works:

<table>
    <tr>
        <td align="center">
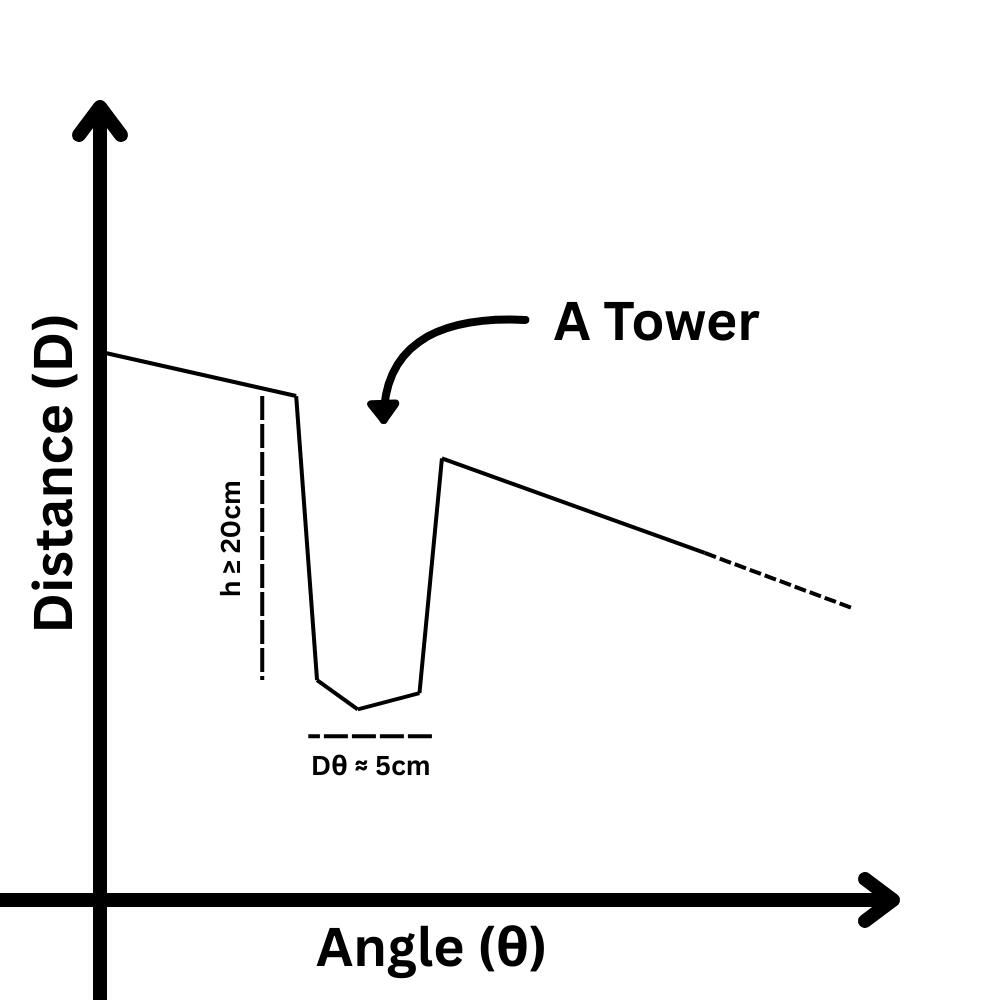
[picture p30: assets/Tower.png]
Tower
            
        </td>
        <td align="center">
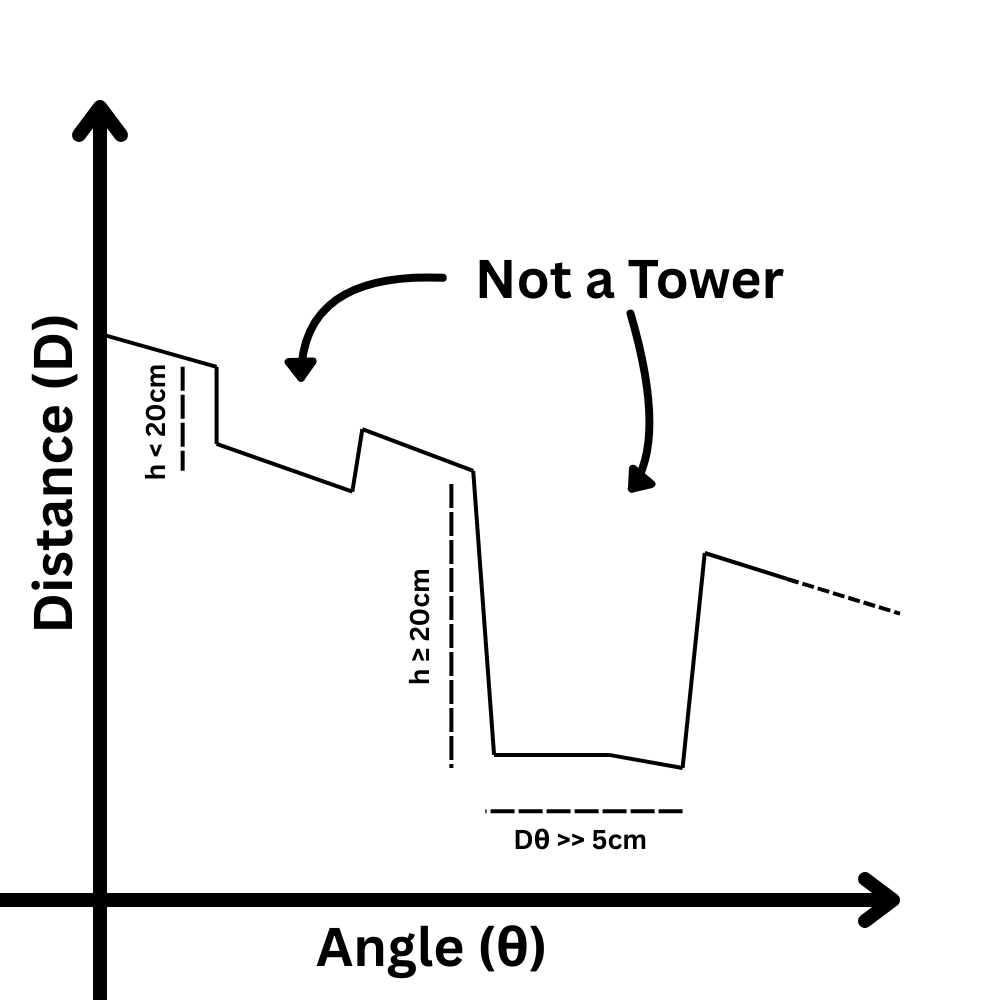
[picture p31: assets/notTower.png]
Not a tower
            
        </td>
    </tr>
    <tr>
        <td align="center"><sub>The valley has a depth of more than 20cm and the calculated size is around 5cm</sub></td>
        <td align="center"><sub>These are not towers because either the valley depth is lower than 20cm, or the calculated size is much different from 5cm.</sub></td>
    </tr>
</table>

```mermaid
flowchart LR
    A[Start LiDAR scan] --> B[Read distance values across rays]
    B --> C[Look for sudden changes in distances]
    C --> D{Spike detected?}
    D -- No --> B
    D -- Yes --> E[Measure width of the detected spike]
    E --> F{Width matches tower size?}
    F -- No --> B
    F -- Yes --> H[Mark as possible tower]
    H --> I[Final tower detection result]
    I --> B[Continue scanning]

```

After detecting the towers, the robot needs to avoid them. The robot needs to move to the left of green objects. So what it does, it imagines a wall at the right of any green tower. That way, the robot is forced to pass the object from the left side. The opposite happens for red towers.

#### Possible Improvement
Currently, the main bottleneck of the robot is the LiDAR. Because it only has a scan rate of 10Hz, speeding up the robot can cause it to miss a lot of data. As the robot's position/odometry can be calculated pretty accurately, and we can also determine the objects' positions accurately as well, it is possible to cache the detected objects in the first lap. Then those cached object positions can be used to safely bump up the robot's speed byt updating those positions based on the robot's odometry. Because the odometry can be updated pretty fast, this can be a good method to speed up the robot.

#### Parking
We thought parking would be very difficult, but it was pretty simple. Moving out of the parking spot was straightforward. Although we had to choose the path based on the color of the first object, it was fairly simple.
However, moving into the parking spot after the run ends - and being parallel on top of that - was no simple matter. But we already had odometry data, motor encoder data and IMU orientation data. All we had to do was first align the robot in a specific arrangement with the parking spot and run a predetermined movement sequence. And that's all it took to complete the parking.

Here's how it works:
<table>
    <tr>
        <td align="center">
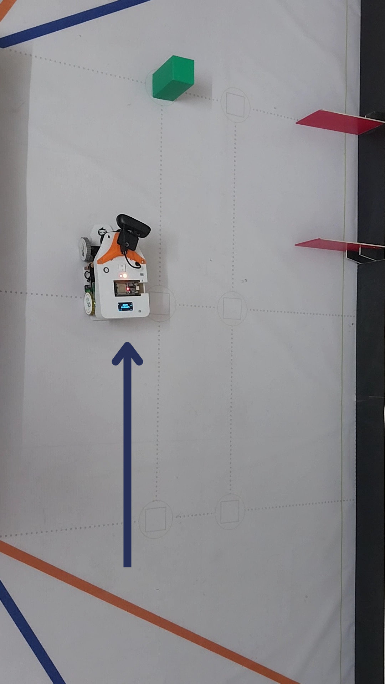
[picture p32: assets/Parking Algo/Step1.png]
Step-One
            
        </td>
        <td align="center">
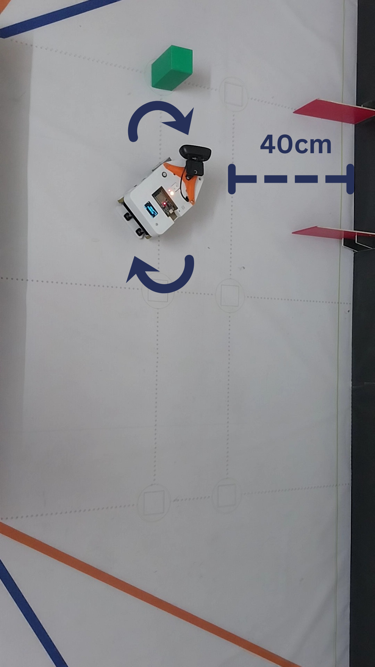
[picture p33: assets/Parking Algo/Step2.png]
Step-Two
            
        </td>
    </tr>
    <tr>
        <td align="center"><sub>The robot stops using the odometry values.</sub></td>
        <td align="center"><sub>The robot turns such a way that it remains around 40cm away from the parking adjacent wall</sub></td>
    </tr>
</table>
<table>
    <tr>
        <td align="center">
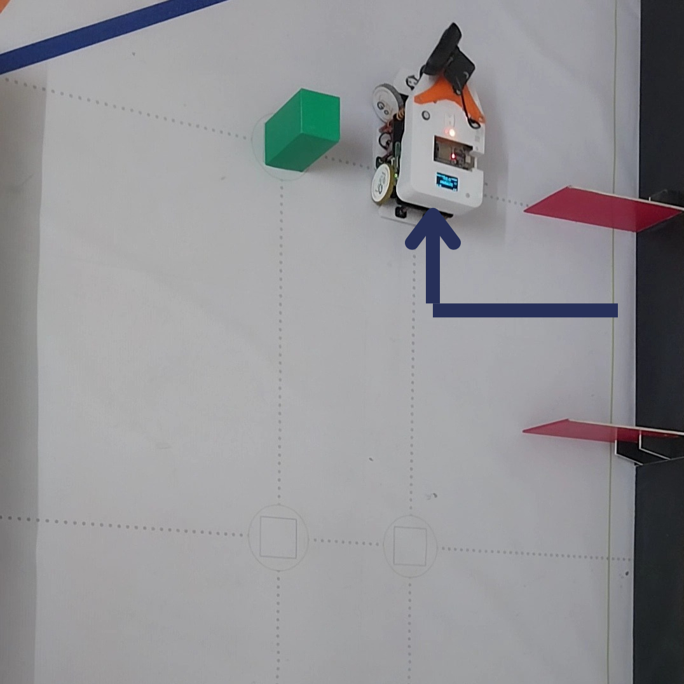
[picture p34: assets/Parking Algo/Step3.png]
Step-Three
            
        </td>
        <td align="center">
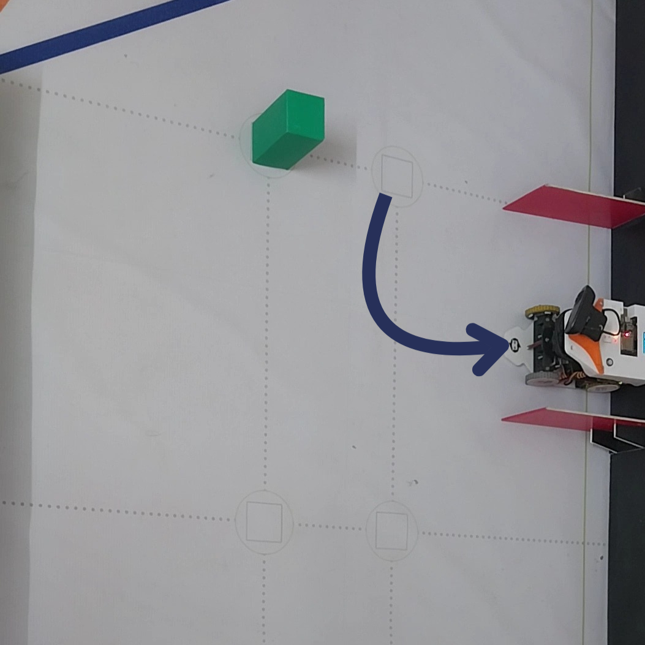
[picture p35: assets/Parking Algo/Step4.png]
Step-Four
            
        </td>
    </tr>
    <tr>
        <td align="center"><sub>The robot moves to a certain position in front of the parking.</sub></td>
        <td align="center"><sub>The robot directly moves into the parking spot</sub></td>
    </tr>
</table>

<table>
    <tr>
        <td align="center">
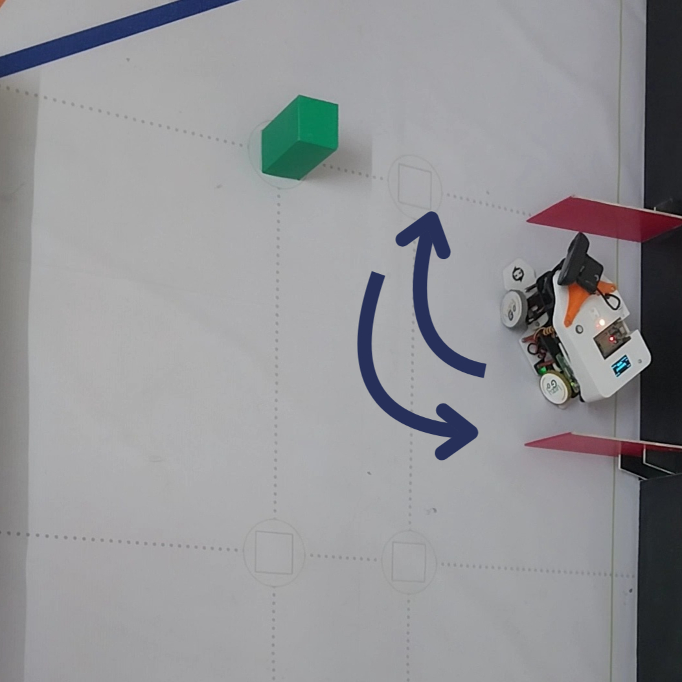
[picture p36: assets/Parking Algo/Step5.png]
Step-Three
            
        </td>
        <td align="center">
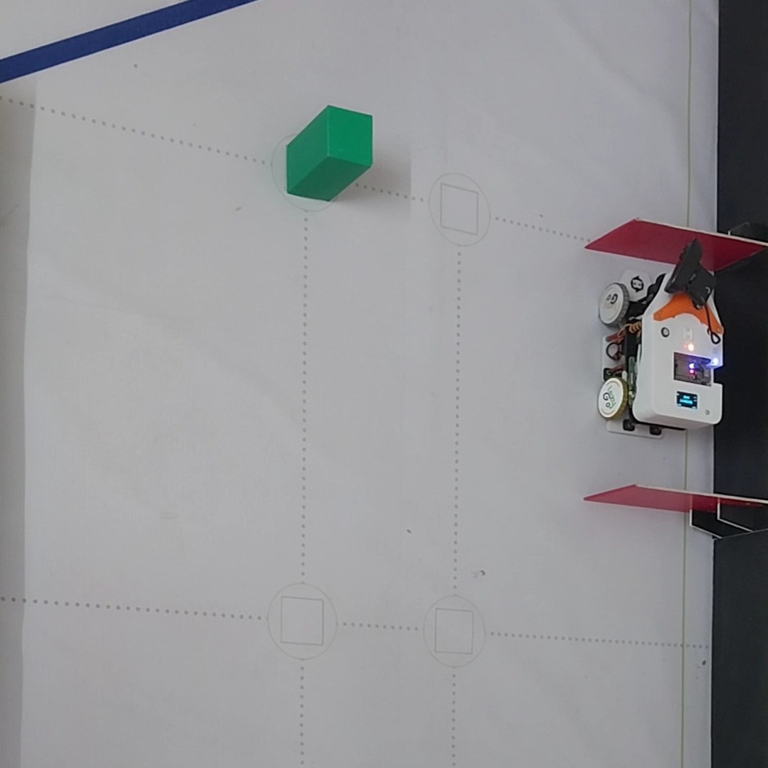
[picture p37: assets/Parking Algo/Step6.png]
Step-Four
            
        </td>
    </tr>
    <tr>
        <td align="center"><sub>From there, it moves back and forth...</sub></td>
        <td align="center"><sub>...Until it is completely straight.</sub></td>
    </tr>
</table>

## Important Note on the Camera

We attached the robot's main camera on a servo motor. Since we are detecting the towers' positions using the LiDAR values, we can easily point the camera towards the closest object using the servo. This makes it super easy to isolate a target tower. And allows us to use a lower Field of View (`FoV`) camera and cover a large area.

#### But does using a low `FoV` camera have any benefits?

Fish eye lenses with high `FoV`s introduce a lot of distortion. It can be fixed by calculating the lens intrinsics and camera matrix coefficients, but that also takes up some processing time as it needs to be done for every frame. It is not too big of an issue if you just need to use color masking with OpenCV. However, there is another issue with high `FoV` cameras. <br><br>
Generally, cameras with a higher `FoV` have lower image brightness (per unit area) if other settings (such as aperture and exposure time) remain the same. This is because the same amount of light gathered by the lens is distributed over a larger sensor area. <br><br>
We can increase the exposure, but that increases motion blur and sometimes even introduces lag. This is an issue especially for the WRO Future Engineers Category. Over the years, we've noticed that the tower colors are usually very dark. This makes it tricky to detect their colors, and differentiate them from the black wall. Here, a camera with more overall brightness will perform better than one with a lower overall brightness. So a low `FoV` camera helps in this sense as well. 

In addition, as we directly point the camera towards a tower, we put the color detection object in the center of the camera field of view, reducing the risk of detecting other things around the robot. Our robot doesn't even look at them! 🗿🗿

> **TL;DR:** Higher `FoV` cameras distribute light over a higher area, reducing overall picture brightness. The LazyBot uses lower `FoV` camera points it at target objects to tackle low light conditions.

Here, see it in action (click for YouTube Video):

<p align="center">
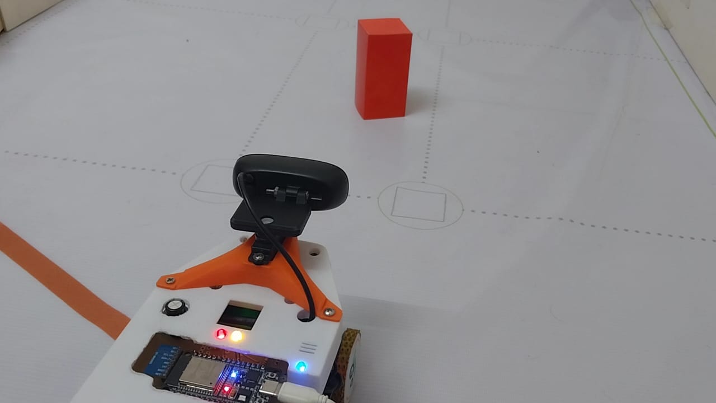
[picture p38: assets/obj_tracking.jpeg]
  
</p>

---

## Gazebo Simulation and Its Role in Our Development Workflow

A significant part of our development process relied on simulation in Gazebo, which allowed us to design, test, and refine our robot’s behavior long before the physical robot was ready. Since mechanical fabrication and electronics assembly take substantial time, we built a fully functional simulated robot in parallel to ensure continuous progress on the software side.

### Why We Used Gazebo

Gazebo offers a high-accuracy 3D physics engine, sensor simulations, and world-building tools, making it ideal for robotics development. For a competition like WRO Future Engineers, where autonomous navigation is heavily dependent on sensor reliability and precise motion control, simulation provides several advantages:

**1. Simulated Track**  
We recreated a close approximation of the WRO track inside Gazebo.  
This included:

   - Track geometry
   - Obstacles
   - Surface color textures
   - Close approximation of our robot's mobility system (Turning radius, speed)

This allowed us to test navigation algorithms in the same conditions the real robot would face during the event.

**2. Early Development Without Hardware**  
While the mechanical and electronics teams were designing and building the physical robot, the software team was able to:
   - Develop the control system
   - Tune parameters
   - Implement the object detection workflow
   - Test odometry and localization
   - Experiment with obstacle avoidance strategies

This parallel workflow significantly reduced development bottlenecks.

**3. Sensor Simulations (LiDAR, IMU, Camera)**  
Gazebo provides realistic sensor plugins that behave similarly to the real hardware:
   - LiDAR: We used Gazebo’s GPU LiDAR plugin to simulate point clouds, allowing us to test our object detection pipeline (shape matching + camera pointing).
   - Camera: We validated our camera servo tracking logic by replaying LiDAR-detected angles in simulation.
   - IMU + Wheel Encoders: These helped us implement and refine our odometry algorithm before deploying it on the physical robot.

This ensured that once the real sensors were installed, our software already had a stable foundation.

**4. Safety and Rapid Iteration**  
Certain tests - such as high-speed turns, collision detection, or repeated obstacle challenges - carry risk of damaging hardware.  
Using simulation, we were able to:
   - Try aggressive parameters safely
   - Run tests repeatedly
   - Introduce random noise to simulate real-world uncertainty
   - Debug without risking mechanical damage

**5. Faster Algorithm Development**  
Simulation enabled:
   - Recording bag files for analysis
   - Visualizing all sensor data in RViz
   - Running thousands of test cycles without hardware fatigue
  
This drastically accelerated the tuning process for:
   - Object detection with LiDAR
   - Disparity-based depth estimation
   - Lap counting logic
   - Obstacle challenge navigation

### Open-Source Simulation Files
To support future WRO teams and contribute to the robotics community, we have made our entire simulation setup fully open source.  
Anyone reading this documentation can:

- Clone our repository
- Launch the Gazebo world
- Load our robot model
- Run all nodes exactly as we did

Modify or extend our system freely. All simulation-related files, including:

- The URDF/Xacro robot model
- Gazebo plugin configurations
- World files
- Launch files
- Navigation scripts

…are available in this repository. You can find detailed instructions on how to setup and use Gazebo with ROS2 [here](../instructions/README.md).

We encourage other teams to use this simulation as a reference or starting point. The goal of WRO Future Engineers is to promote learning and share knowledge openly, and we are proud to contribute back to the community.

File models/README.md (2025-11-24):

## Robot Design Overview
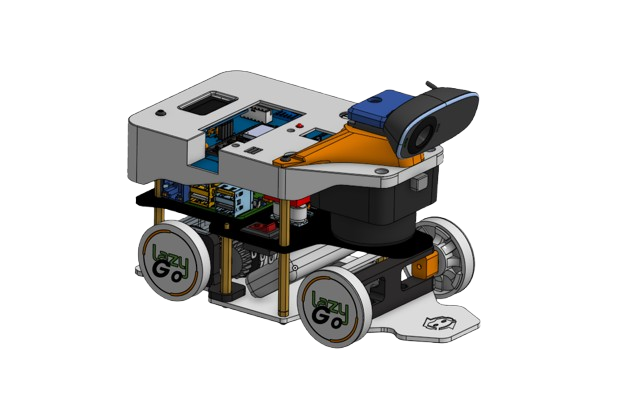
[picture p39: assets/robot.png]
 
 
Our robot was fully designed in **Onshape**, enabling seamless collaboration and easy replication through a shared project link. The mechanical structure was developed with a core objective:

> **Achieve an extremely tight turning radius while maintaining excellent balance and traction.**

To reach this goal, we combined a **differential drive system** with **Ackermann steering**, allowing sharp, controlled turns **without wheel slip**—significantly improving odometry accuracy.

The robot fits within a **20 cm × 10 cm footprint** with a **wheelbase of 11.5 cm**, and through geometric steering angle calculations, we successfully achieved a **turning radius below 15 cm**.

---
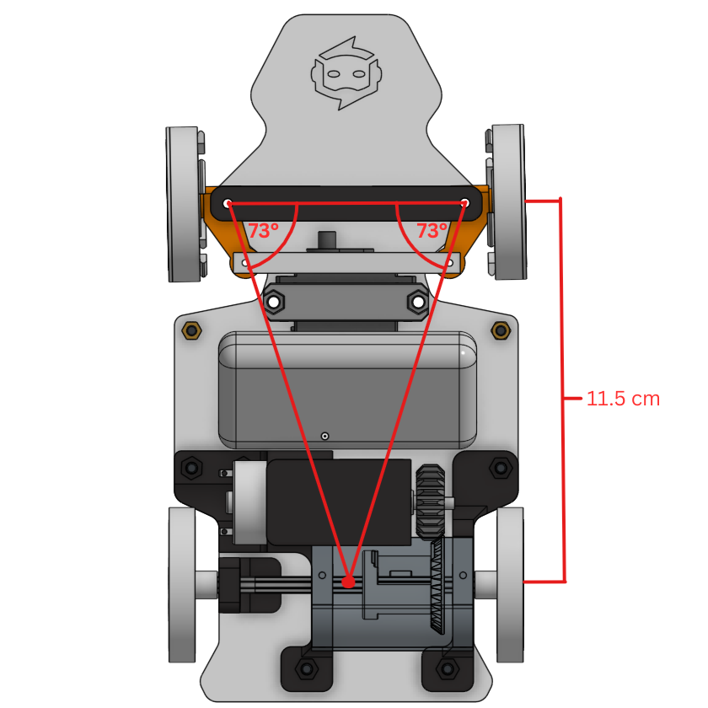
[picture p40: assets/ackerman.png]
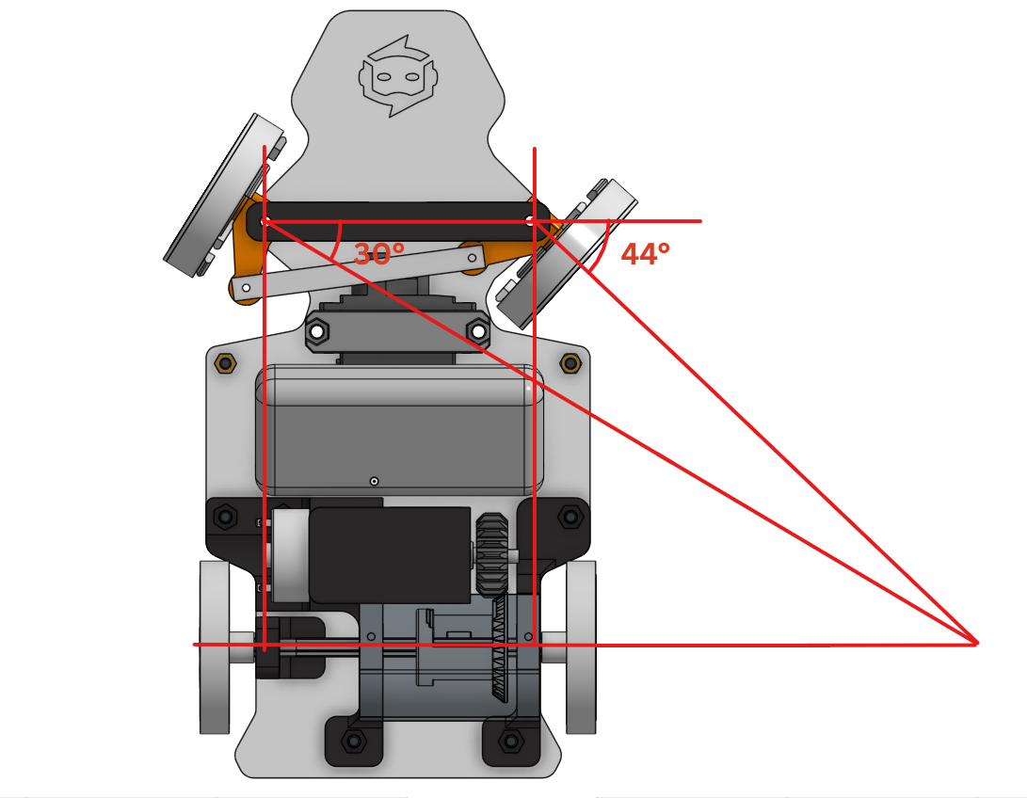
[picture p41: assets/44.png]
<p align="center"> <p/>
The Ackermann geometry was designed by projecting steering axis and wheel intersection lines and shaping the linkage based on the resulting steering angles.

Here is our Onshape project link:  [Onshape CAD Project](https://cad.onshape.com/documents/0ec023d9700593bfeebabdea/w/02e5710fbedd7baee1480c4a/e/63f1a3919addf09c73a6e4d6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)

---

### Modular Three-Stage Structure

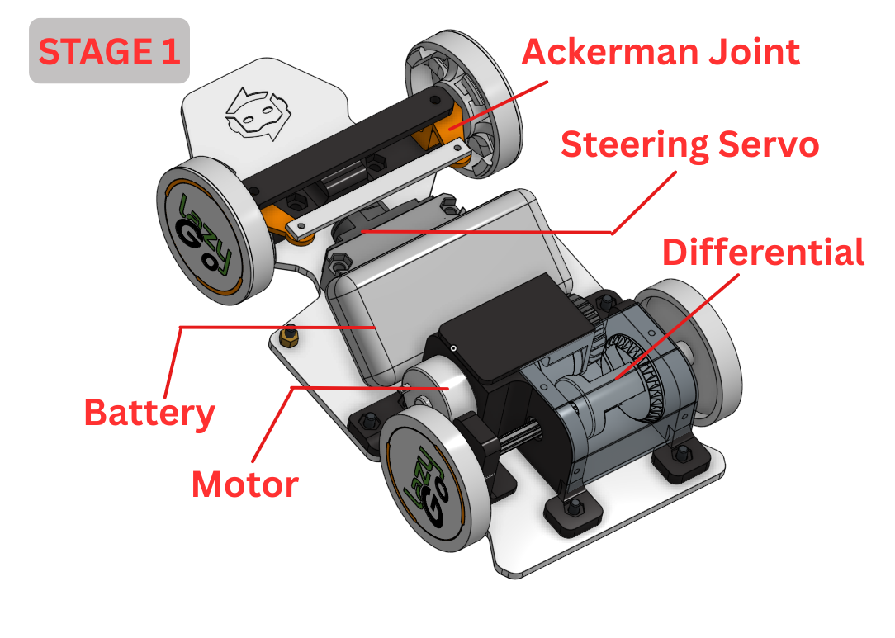
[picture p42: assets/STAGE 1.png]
 
 
To maximize maintainability and simplify repairs, the robot is constructed in **three stacked stages**:

#### Stage 1 – Base Chassis
- Drive motors and actuators  
- Battery compartment  
- Low center of gravity for stability  

---

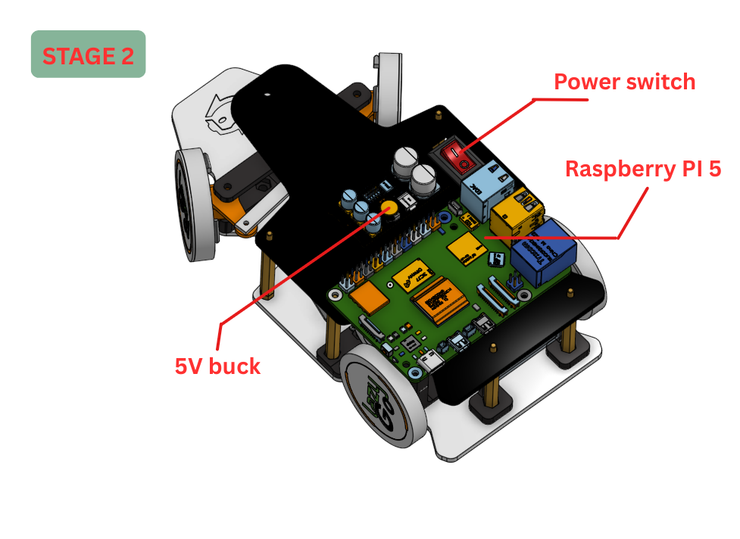
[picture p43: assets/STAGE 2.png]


#### Stage 2 – Control Platform 
- Raspberry Pi main computing unit  
- 5V 5A buck converter  
- Reserved front clearance for the LiDAR
- Motor driver mounted beneath the plate

---

#### Stage 3 – Electronics & Interface Layer
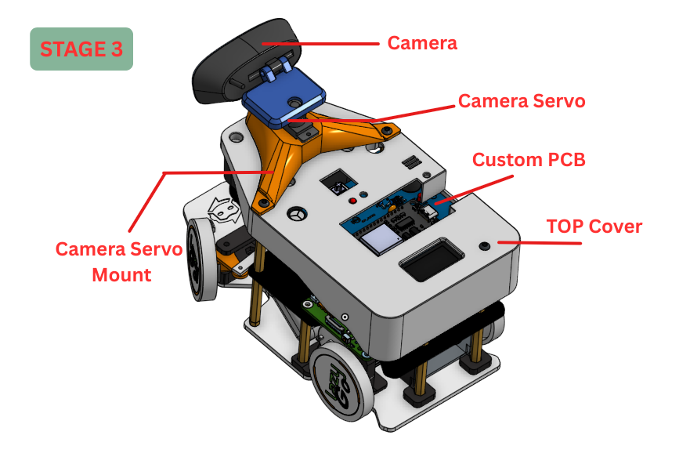
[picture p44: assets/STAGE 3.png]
- Custom PCB with secondary microcontroller   
- IMU and onboard OLED display  
- 3D-printed protective shell that:
  - holds the LiDAR upside down at **5 cm height** for accurate wall and obstacle sensing  
  - protects the electronics  
  - enhances the robot’s appearance  

---
---

### Camera Head 
<p align="center">
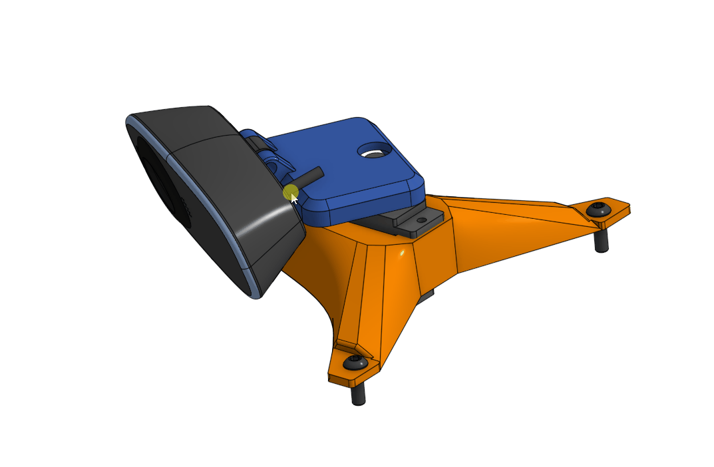
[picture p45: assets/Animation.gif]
  
</p>

Mounted at the top is a **servo-controlled camera**, giving the robot a dynamic, head-like field of view.  
For a tactile interaction point, we incorporated a **mechanical switch** as the main start trigger.

---

### Design Philosophy

While our primary objective is **reliable mission performance**, we also believe that:

> **If the robot can look awesome while working flawlessly — why not embrace both?**
---
---
## 3D Printing Guide

Our robot consists of **22 individual STL models**, with only **three parts requiring two prints each**. Most components can be printed using standard settings, but a few pieces benefit from special preparation due to mechanical fit, bearings, and multi-color detailing.

### Recommended Print Settings
- **Layer height:** 0.2 mm (adaptive layer height recommended for curved or detailed parts like the camera servo mount)
- **Infill:** ~20% (gyroid or cubic suggested)
- **Supports:** Standard support angle works for most parts
- **Bridging:** Performs well on nearly all models
- **Perimeters:** 3 walls for stronger screw-mount areas

### Front Wheel Bearing Insertion
The **front wheel parts include an integrated 625 bearing seat**.  
To print these correctly:

1. Start the print **without supports** (bearing housing must remain clean)
2. Pause the print at **7 mm height**
3. Insert the **625 bearing**
4. Resume printing—the upper layers will lock the bearing in place

This ensures smooth rolling and perfect concentric alignment.

### Multi-Color Components
Some parts are designed for color separation, including:
- Rear wheels  
- Front wheels  
- Bottom chassis plate  

If you prefer **single-color printing**, simply slice the STL normally and ignore color segmentation.

### Slicer & Printer Notes
We printed all components on a **Bambu Lab P1S** with AMS, giving us:
- precise tolerances  
- clean multicolor transitions  
- consistent dimensional accuracy  

All slicing was performed in **Bambu Studio**.  
If you are using the same printer and want to skip slicing setup, you can download our **pre-sliced project files** from our MakerLab profile (linked in this repository).

### Additional Printing Tips
- **Dry your filament**—better tolerances and cleaner overhangs  
- **PLA+ or PETG** recommended for durability  
- **Slow down first-layer speed** for better bed adhesion  
- **Test-fit before full assembly** to avoid overly tight tolerances  
- **Label parts during printing** to simplify sorting  

These guidelines ensure strong, dimensionally accurate parts that assemble smoothly with the mechanical system.

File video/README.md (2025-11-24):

# Robot Explanation
You can watch this following video to know a little bit about our team and robot. It also contains a, assembly video at the end, so don't miss it!

<div align="center">
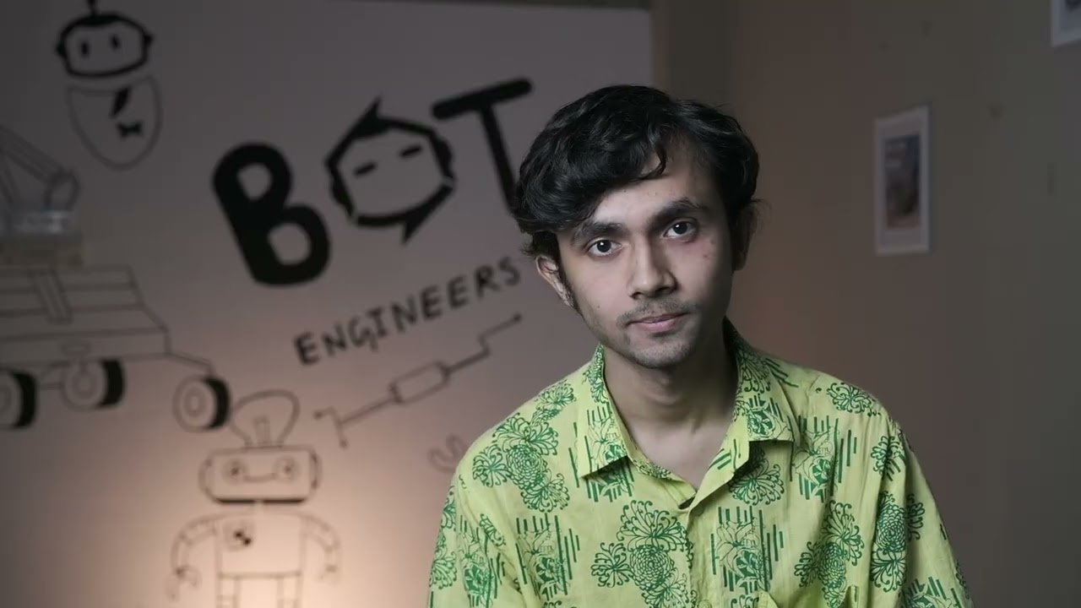
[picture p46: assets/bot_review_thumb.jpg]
  
</div>

---
---

# Performance Videos
Performance videos of our robot during the Open Challenge and the Obstacle Challenge:

<table>
    <tr>
        <td align="center">
            <a href="https://youtu.be/CT9NGIUzYoM">
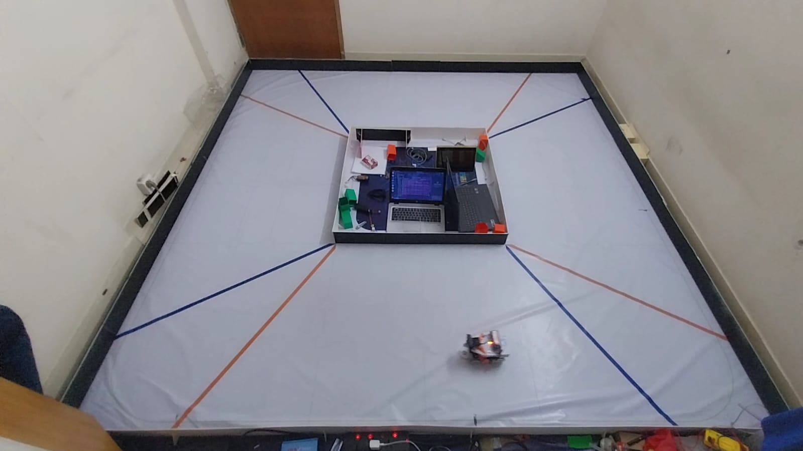
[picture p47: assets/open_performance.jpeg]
Open Challenge Performance Video
                
            </a>
        </td>
        <td align="center">
            <a href="https://youtu.be/3PXJUEEfc3k">
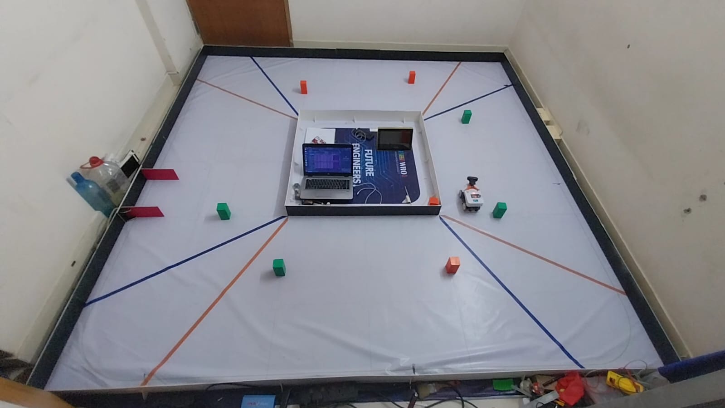
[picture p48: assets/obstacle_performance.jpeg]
Obstacle Challenge Performance Video
                
            </a>
        </td>
    </tr>
    <tr>
        <td align="center"><sub>Open Challenge Performance Video</sub></td>
        <td align="center"><sub>Obstacle Challenge Performance Video</sub></td>
    </tr>
</table>

# Simulation Videos
Initially, we implemented all the logic on a simulated robot. Here are some screen recordings of those simulations:

<table>
    <tr>
        <td align="center">
            <a href="https://youtu.be/7jhgtUxxIgY">
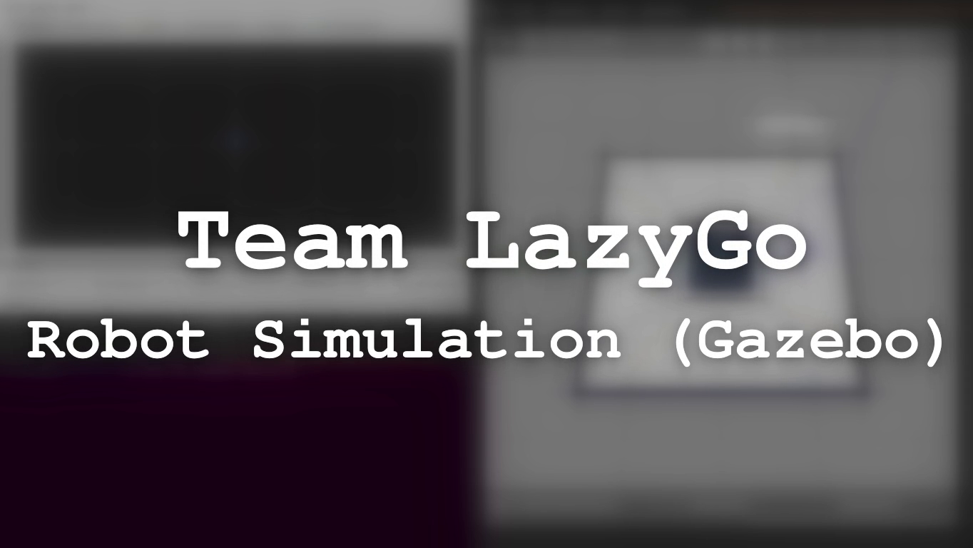
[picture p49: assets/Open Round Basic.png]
Open Round Basic
                
            </a>
        </td>
        <td align="center">
            <a href="https://youtu.be/7BVIbg3AUaY">
                Open Round With Lap Count
            </a>
        </td>
        <td align="center">
            <a href="https://youtu.be/xk6vUA5FqXY">
                Obstacle Round
            </a>
        </td>
        </tr>
    <tr>
        <td align="center"><sub>Open round, without lap count</sub></td>
        <td align="center"><sub>Open round, with lap count</sub></td>
        <td align="center"><sub>Obstacle round</sub></td>
    </tr>
</table>

# Additional Videos
Here are a few videos demonstrating different aspects of our robot:

<table>
    <tr>
        <td align="center">
            <a href="https://youtu.be/CT9NGIUzYoM">
                Object Tracking using LiDAR
            </a>
        </td>
        <td align="center">
            <a href="https://youtu.be/3PXJUEEfc3k">
                Parking
            </a>
        </td>
    </tr>
    <tr>
        <td align="center"><sub>We're using LiDAR to detect the position of the objects. This video demonstrates that. Find more <a href="../src/README.md/#important-note-on-the-camera">here...</a></sub></td>
        <td align="center"><sub>This video demonstrates our parking approach for the obstacle round. Learn more about this <a href="../src/README.md/#parking">here...</a></sub></td>
    </tr>
</table>

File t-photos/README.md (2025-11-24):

# Team Photos
All three of our team members have previously participated in international rounds. Here's a picture of us together:


> Unfortunately, currently Prithul is outside of Bangladesh, and we kind of forgot to take any group photo with all three of us together. So, he was digitally added in 😛

---

Noor and Rakibul, blending in with the environment because the robot is running 😛



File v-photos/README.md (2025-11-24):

# Vehicle Photos
Our robot, from every directions - no secrets! ^-^

| Front | Back |
| --- | --- |
| front | back |

| Top | Bottom |
| --- | --- |
| top | bottom |

| Left | Right |
| --- | --- |
| left | right |

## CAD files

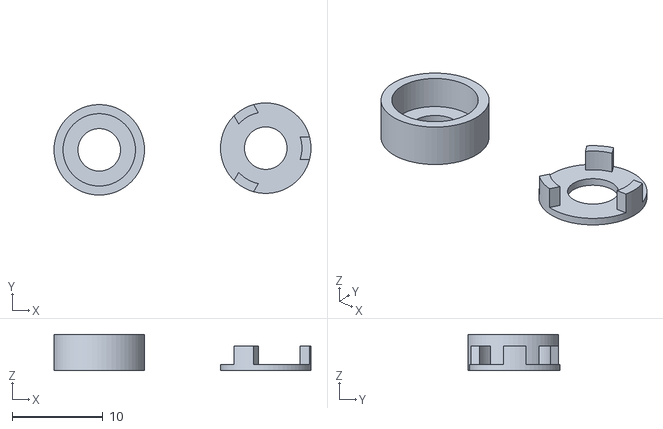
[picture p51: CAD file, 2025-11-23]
models/gearbox support right.stl
28.4 x 10.2 x 4.00

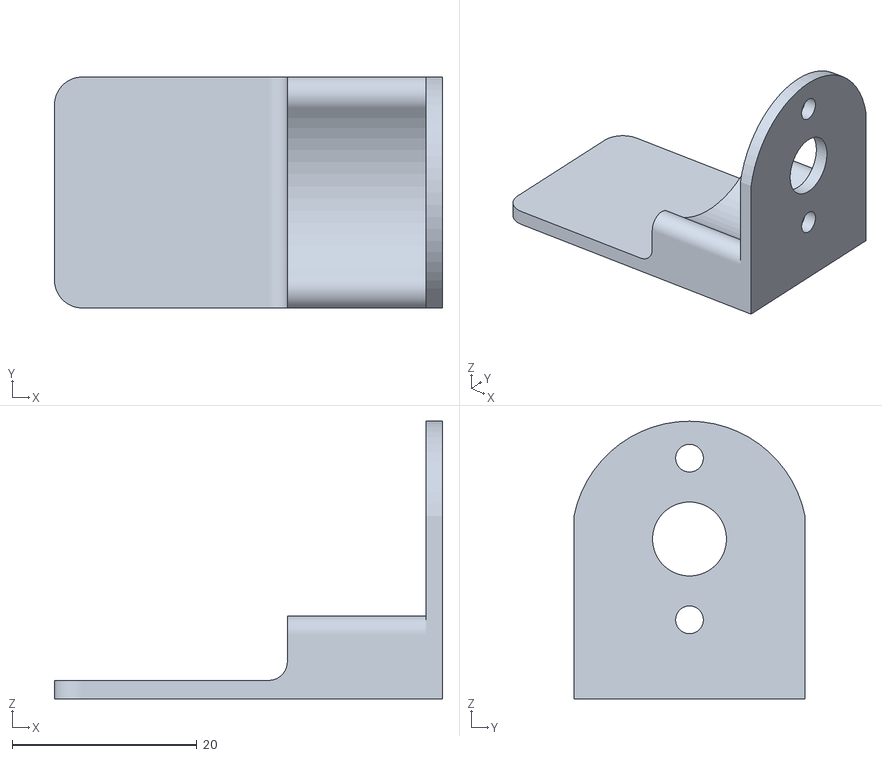
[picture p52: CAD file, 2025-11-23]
models/motor mount-.stl
42.0 x 25.0 x 30.0

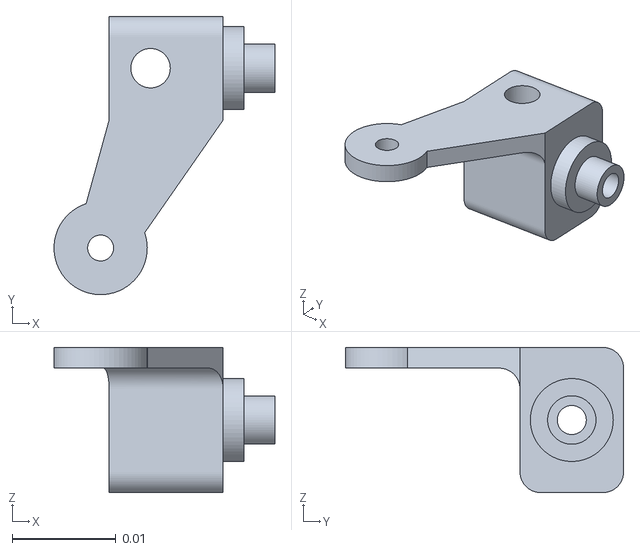
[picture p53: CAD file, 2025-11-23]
models/steering lever right.stl
0.0213 x 0.0268 x 0.014

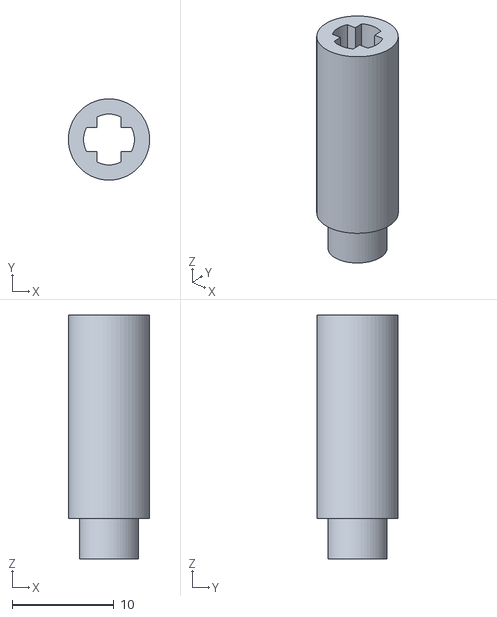
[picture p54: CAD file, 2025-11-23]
models/lego shaft lock left.stl
8.00 x 7.99 x 24.0

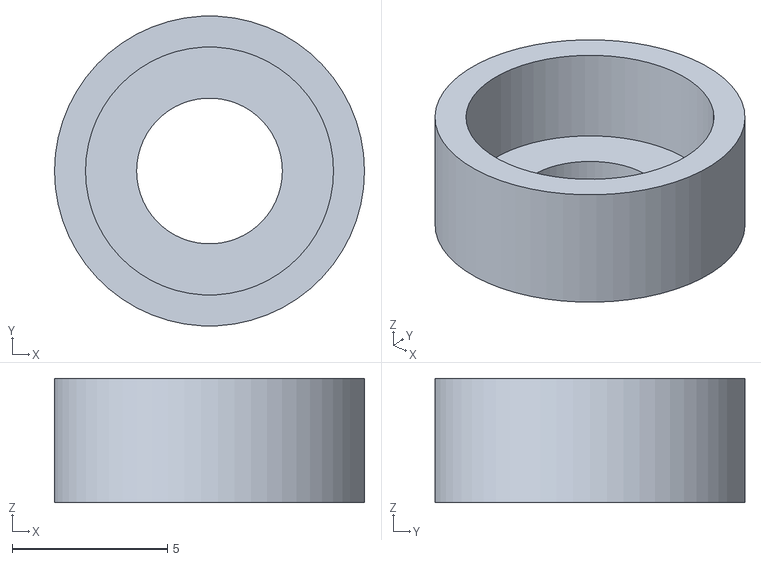
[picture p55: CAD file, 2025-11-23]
models/gearbox support left - 1.stl
10.0 x 9.99 x 4.00

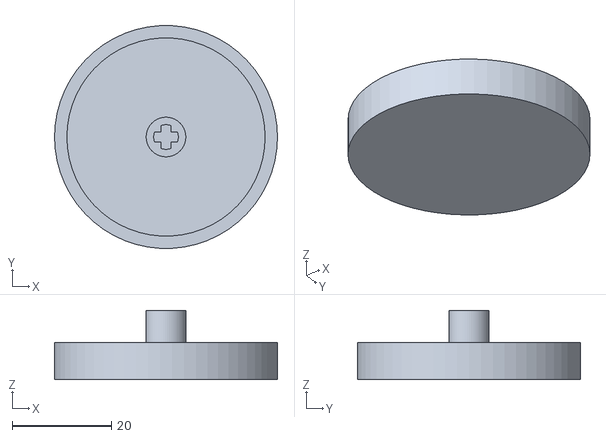
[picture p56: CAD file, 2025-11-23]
models/Rear wheel- x2.stl
45.0 x 44.9 x 14.0

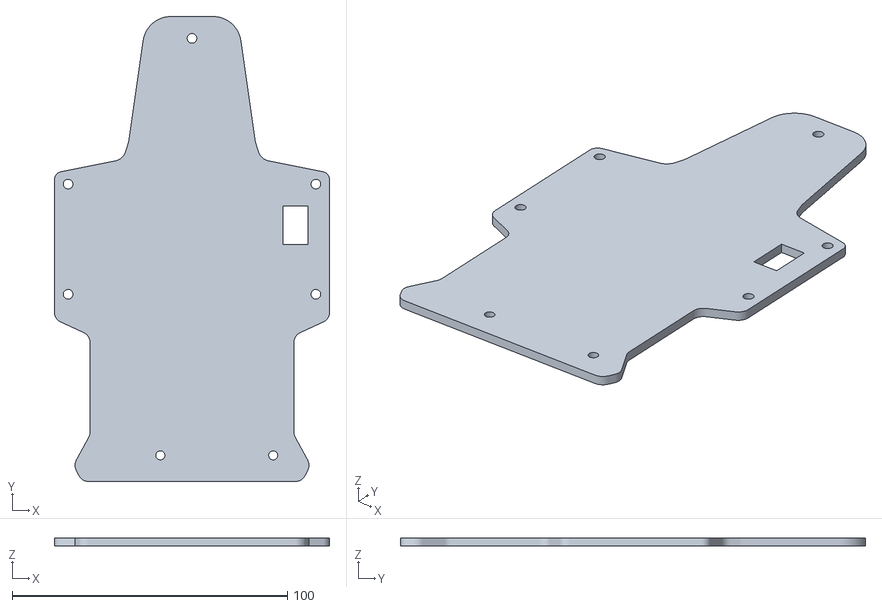
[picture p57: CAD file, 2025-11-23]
models/base plate 2nd layer.stl
100.0 x 168.9 x 3.00

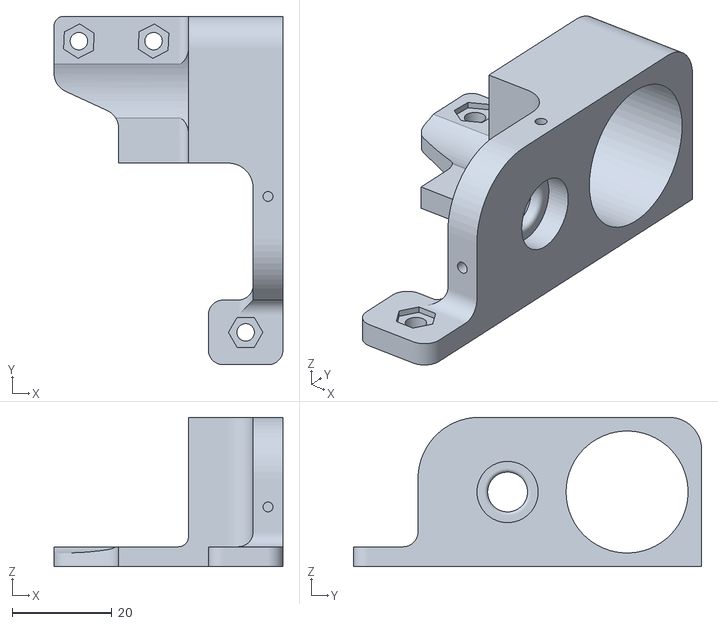
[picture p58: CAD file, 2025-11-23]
models/motor body and differential holder left.stl
46.0 x 70.0 x 30.0

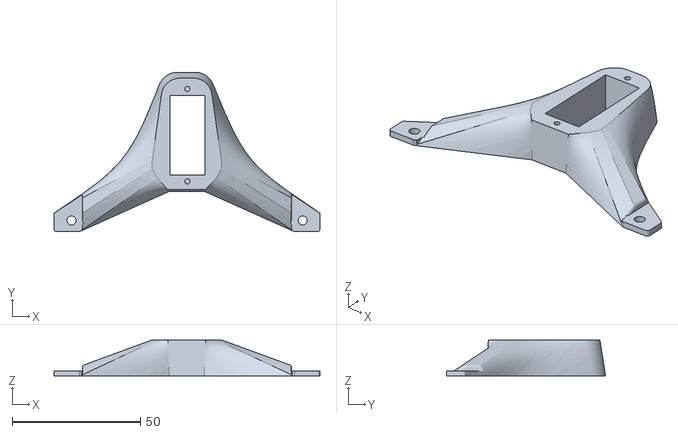
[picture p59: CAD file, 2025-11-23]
models/camera servo holder(PS1171MG).stl
103.6 x 62.0 x 14.0

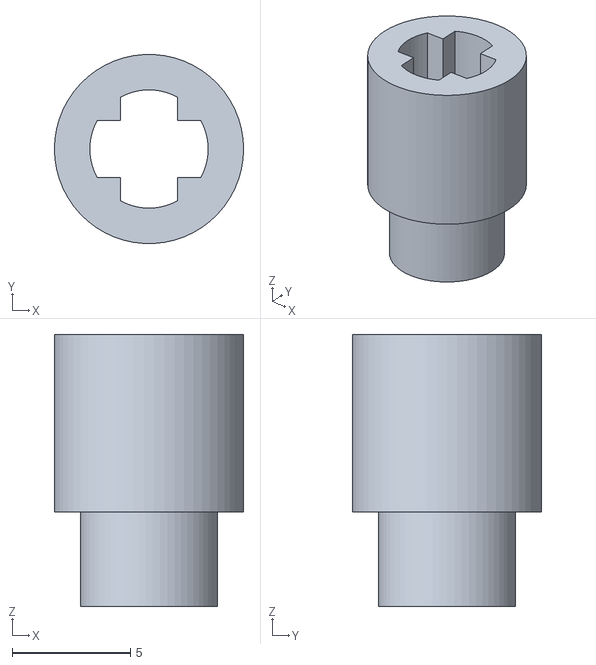
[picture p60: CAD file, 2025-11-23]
models/gearbox support left -2.stl
8.00 x 7.99 x 11.5

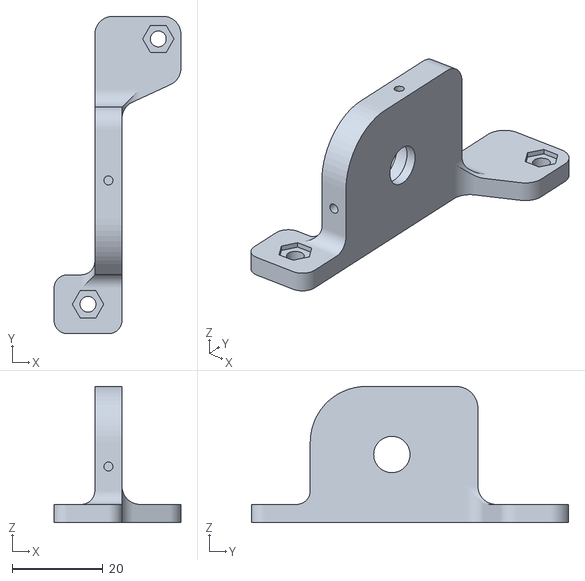
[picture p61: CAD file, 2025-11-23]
models/differential holder right.stl
28.0 x 70.0 x 30.0

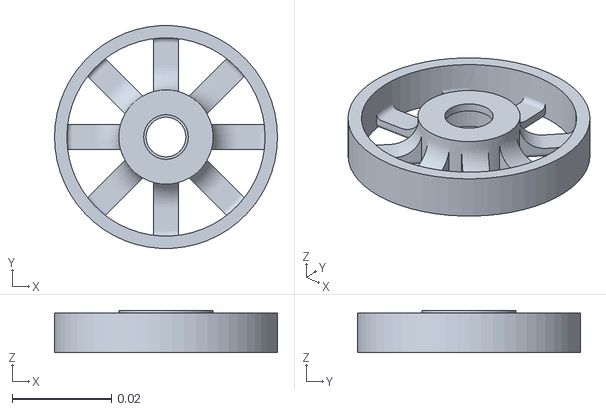
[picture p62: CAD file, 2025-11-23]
models/front wheel - x2.stl
0.045 x 0.0449 x 0.0085

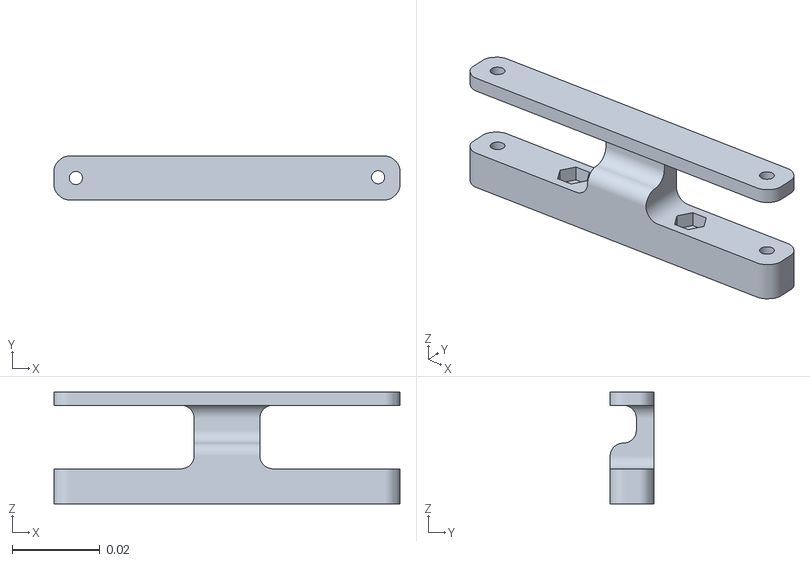
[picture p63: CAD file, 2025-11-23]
models/steering rack.stl
0.079 x 0.01 x 0.0255

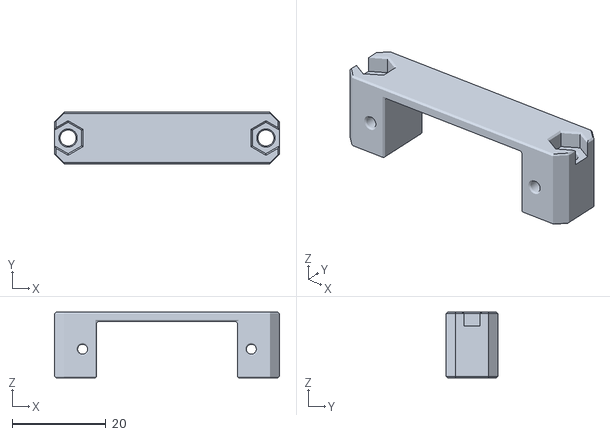
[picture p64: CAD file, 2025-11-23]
models/PS-1171mg Servo Mount.stl
48.0 x 11.0 x 14.0

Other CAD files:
models/Front wheel cover- x2.stl
models/lego shaft lock right.stl
models/CarTop Cover-.stl
models/camera holder-.stl
models/PS1171MG Servo-Arm.stl
models/bottom chassis-.stl
models/read axel support left.stl
models/steering lever left.stl

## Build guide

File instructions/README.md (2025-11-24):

# Instructions
Want to use this package for your robot? Or maybe you just want to use the simulator? You can find the instructions here.







Hey! If you have any trouble, you may want to check out the [Issues](https://github.com/A-N-M-Noor/LazyGo_WRO2025/issues?q=is%3Aissue%20state%3Aclosed) page and find if there's any solution there.

## Installing Ubuntu
As we are using ROS2 for our robot, we installed Ubuntu on our Pi. Now, it is completely possible to use ROS2 without using Ubuntu, just on a Pi OS using Docker. But to keep things simple, we decided to install Ubuntu on our Pi.

#### Which version?
You can either use ROS2 Humble with Ubuntu 22.04, or you can use ROS2 Jazzy with Ubuntu 24.04.

There is no direct download link for Ubuntu 22.04 for ARM architecture (Please let us know if you find any). And you can't install Ubuntu 22.04 from Pi Imager for a Pi 5. Therefore, we are using ROS2 Jazzy with Ubuntu 24.04. But this version of Ubuntu comes with a few problems. For example, you'll face a lot of issues installing a working VNC here. But thankfully ROS2 comes with a lot of remote debugging tools. And you can even code inside VSCode with its remote SSH feature. So you probably won't even need any VNC.

#### Installation
Download the Official Ubuntu Image for ARM from [here](https://cdimage.ubuntu.com/daily-live/20240421/). Download the `64-bit ARM (ARMv8/AArch64) desktop image` iso file.

Install Raspberry Pi Imager from [here](https://www.raspberrypi.com/software/). Use the imager to burn the image file to an SD card. Or you can use any other image writing software of your choice.

Insert the SD card into the Pi, and turn it on. The first time you'll need to use a monitor.

## Installing Packages
#### Pip3

```
sudo apt install python3-pip
```

#### Git
```
sudo apt install git-all
```

#### VSCode (Optional)
```
wget https://update.code.visualstudio.com/latest/linux-deb-arm64/stable -O code_arm64.deb
```
```
sudo apt install ./code_arm64.deb
```

## Installing ROS2
You can find all the instructions on the official [ROS2 website](https://docs.ros.org/en/jazzy/Installation/Ubuntu-Install-Debs.html).

#### UTF8
First, check if you have UTF8
```
locale
```
If you don't have it,
```
sudo apt update && sudo apt install locales
sudo locale-gen en_US en_US.UTF-8
sudo update-locale LC_ALL=en_US.UTF-8 LANG=en_US.UTF-8
export LANG=en_US.UTF-8
```
Then verify again.

#### APT Repository
Ensure that the Ubuntu Universe repository is enabled.
```
sudo apt install software-properties-common
sudo add-apt-repository universe
```

.

Add the ROS2 APT repository
```
sudo apt update && sudo apt install curl gnupg lsb-release
sudo curl -sSL https://raw.githubusercontent.com/ros/rosdistro/master/ros.asc -o /usr/share/keyrings/ros-archive-keyring.gpg
```
```
echo "deb [arch=$(dpkg --print-architecture) signed-by=/usr/share/keyrings/ros-archive-keyring.gpg] http://packages.ros.org/ros2/ubuntu $(lsb_release -cs) main" | sudo tee /etc/apt/sources.list.d/ros2.list > /dev/null
```

#### Installation - ROS2 Jazzy Jelisco
Install ROS2 Jazzy Jelisco
```
sudo apt update
sudo apt install ros-dev-tools ros-jazzy-desktop
```

.

Install `colcon` for building ROS2 projects
```
sudo apt install python3-colcon-common-extensions
```

.

Install and initialize rosdep
```
sudo apt install python3-rosdep python3-vcstool build-essential
```
```
sudo rosdep init
rosdep update
```

#### Source some files
Add ROS2 and colcon to the ~/.bashrc file, so that theyare sourced on every terminal. Adding colcon will enable autocomplete of commands.

First, open the .bashrc file
```
sudo nano ~/.bashrc
```
At the end, add these lines:
```
source /opt/ros/humble/setup.bash
source /usr/share/colcon_argcomplete/hook/colcon-argcomplete.bash
```

## Installing Gazebo
If you want to run the simulation, you'll need to install Gazebo.

> [!WARNING]  
> Do not try to run the simulation on your Raspberry Pi!

To use the simulation, you should install ROS2 on a separate PC/Laptop and run the simulation there.

> We already had ROS2 Humble installed on a separate device, so we used that version to run the simulation. You can install the new ignition gazebo with ROS2 Jazzy. But we used Gazebo Classic 11 with ROS2 Humble ([Installation guide here](https://docs.ros.org/en/humble/Installation/Ubuntu-Install-Debs.html)).

After you have ROS2 Humble working on your device...

First, install Gazebo
```
sudo apt update
sudo apt install ros-humble-gazebo-ros-pkgs ros-humble-gazebo-ros
```
Source the gazebo bash file
```
source /usr/share/gazebo/setup.sh
```

You should be able to run Gazebo using
```
ros2 launch gazebo_ros gazebo.launch.py
```

## Use our codes

First, clone our repository
```
git clone https://github.com/A-N-M-Noor/LazyGo_WRO2025.git
```
Head into the repo
```
cd LazyGo_WRO2025
```
Install the required python packages
```
pip3 install -r requirements.txt
```
If pip3 refuses to install the packages, use this command (Only on the Pi. Ideally you would want to create a virtual environment if you're doing this on your everyday device)
```
pip3 install -r requirements.txt --break-system-packages
```

Then build the packages
```
colcon build
```

Before you can run any packages, you'll need to source the workspace
```
source install/setup.bash
```

To run the simulation
```
ros2 launch lazysim gazebo.lazyBot.launch.py
```

This command will launch Gazebo simulator with an URDF model along with RVIZ with lidar and odom data. If you don't want to visualize odom, set the `Fixed Frame` in rviz from `odom` to `base_link`.

Now, edit -
- `/src/lazysim/config/track.yaml` to change the track.
- `/src/lazysim/config/lazySim.rviz` to change the rviz visualization.
- `/src/lazysim/description` files to edit the robot model.

## Package Usage Guide

### Package Overview

#### 1. `lazy_interface`
**Purpose**: Custom ROS2 message definitions for robot communication
- Contains custom message types used across all nodes
- Includes tower detection info, LiDAR data, and debug information
- **No direct launch required** - automatically built with other packages

#### 2. `lazybot` 
**Purpose**: Main control package for the physical robot
- Contains all control logic, sensor processing, and robot behavior
- Handles both open challenge and obstacle avoidance scenarios

#### 3. `lazysim`
**Purpose**: Gazebo simulation environment
- Provides virtual testing environment before deploying to physical robot
- Includes track generation and robot model visualization

#### 4. `ESP32 Code`
**Purpose**: Low-level motor control and sensor interfacing
- PlatformIO project for ESP32 microcontroller
- Handles motor control, encoders, IMU, and parking maneuvers

---

### Launch File Usage Guide

#### For Physical Robot Testing

##### **Open Challenge** (3 laps without obstacles)
```bash
ros2 launch lazybot open.lazy_launch.py
```
**What it launches**: 
- Control node for the open challenge rounds
- Serial node for ESP32 communication
- Debug node for visualization
- RPLiDAR C1 driver Node

##### **Obstacle Challenge** (3 laps with tower avoidance + parking)
```bash
ros2 launch lazybot robot.lazy_launch.py
```

**What it launches**:
- Control node for obstacle avoidance
- Parking node for parking logic
- Detection node for camera-based tower detection
- Serial node for ESP32 communication
- Debug node for visualization
- RPLiDAR C1 driver Node

---

#### For Simulation Testing

##### **Full Gazebo Simulation**
```bash
ros2 launch lazysim gazebo.lazyBot.launch.py
```
Or this one if you don't want to launch rviz:
```bash
ros2 launch lazysim gazebo.lazyBot.launch.py disable_rviz:=true
```

**When to use**:
- Algorithm development and testing
- Safe testing without physical robot
- Visualizing robot behavior in RVIZ

**What it launches**:
- Gazebo physics simulation with custom world
- Robot URDF model spawning
- Bridge node for Gazebo↔ROS communication
- Track creator node for dynamic track generation
- RVIZ2 for visualization (optional: `disable_rviz:=true`)
- ROS2 control systems

**Configuration**:
- Edit `track.yaml` to modify track layout
- Edit `lazySim.rviz` for visualization settings

##### **Simulation Control Only**
```bash
ros2 launch lazybot sim.lazy_launch.py
```
**When to use**:
- Running control logic in simulation after Gazebo is already launched
- Testing specific algorithms without restarting simulation

**What it launches**:
- Control node for robot control.
- Detection node for simulated detection
- Debug node for visualization

##### **Visualization Only**
```bash
ros2 launch lazysim rviz_lazySim.launch.py
```
**When to use**:
- Viewing debug data from physical robot
- Monitoring robot state without simulation
- Analyzing recorded data

---

### Usage Workflow

#### 1. **Development Phase** 
```bash
# Start with simulation for safe testing
ros2 launch lazysim gazebo.lazyBot.launch.py

# Test control algorithms
ros2 launch lazybot sim.lazy_launch.py
```

#### 2. **Physical Robot Testing**
```bash
# Basic navigation testing
ros2 launch lazybot open.lazy_launch.py

# Full competition testing  
ros2 launch lazybot robot.lazy_launch.py
```

#### 3. **Color Calibration** (Separate utility)
```bash
# For camera-based tower detection tuning
ros2 run lazybot color_calibration_node
```

#### 4. **Debug Visualization**
```bash
# View robot data in RVIZ (works with physical robot)
ros2 launch lazysim rviz_lazySim.launch.py
```

---

### Hardware Dependencies

- **LiDAR**: RPLiDAR C1 (auto-detected via CP2102N USB bridge)
- **Camera**: Logitech C270 for tower detection
- **ESP32**: Connected via serial for motor control and sensors
- **IMU**: BNO055 for orientation tracking

### Key Configuration Files

- `lazysim/config/track.yaml`: Simulation track layout
- `color_data.yaml`: Color detection parameters (Can be generated from the calibration node)

---

Good luck! Do reach out if you face any issue.

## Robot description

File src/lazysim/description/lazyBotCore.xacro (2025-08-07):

<?xml version="1.0"?>

<robot xmlns:xacro="http://www.ros.org/wiki/xacro" name="lazyBot">
    <material name="black">
        <color rgba="0.2 0.2 0.2 1." />
    </material>

    <material name="red">
        <color rgba="1.0 0.0 0.0 1.0" />
    </material>

    <material name="blue">
        <color rgba="0.3 0.57 1. 1." />
    </material>

    <!-- Wheel macro -->
    <xacro:macro name="wheel_link" params="name radius length mass">
        <link name="${name}">
            <visual>
                <geometry>
                    <cylinder radius="${radius}" length="${length}" />
                </geometry>
                <material name="black" />
                <origin rpy="0 0 0" />
            </visual>
            <collision self_collide="false">
                <geometry>
                    <cylinder radius="${radius}" length="${length}" />
                </geometry>
                <origin rpy="0 0 0" />
                <surface>
                    <friction>
                        <ode>
                            <mu>1.0</mu>
                            <mu2>1.0</mu2>
                        </ode>
                    </friction>
                </surface>
            </collision>
            <inertial>
                <mass value="${mass}" />
                <inertia ixx="${(mass/12)*(3*radius*radius + length*length)}" iyy="${(mass/12)*(3*radius*radius + length*length)}" izz="${(mass/2)*radius*radius}" ixy="0" ixz="0" iyz="0" />
                <origin rpy="0 0 0" />
            </inertial>
        </link>
    </xacro:macro>

    <!-- <joint name="base_footprint_joint" type="fixed">
        <parent link="base_footprint"/>
        <child link="base_link"/>
        <origin xyz="0 0 0" rpy="0 0 0"/>
    </joint>

    <link name="base_footprint"> </link> -->
    <link name="base_link"> </link>

    <link name="chassis">
        <visual>
            <origin xyz="${length/2-len_offs} 0 ${ground_offset+height/2}" />
            <geometry>
                <box size="${length} ${width} ${height}" />
            </geometry>
            <material name="blue" />
        </visual>
        <collision self_collide="false">
            <origin xyz="${length/2-len_offs} 0 ${ground_offset+height/2}" />
            <geometry>
                <box size="${length} ${width} ${height}" />
            </geometry>
        </collision>
        <inertial>
            <origin xyz="${length/2-len_offs} 0 ${ground_offset+height/2}" />
            <mass value="${base_mass}" />
            <inertia ixx="${(base_mass/12)*(width*width + height*height)}" iyy="${(base_mass/12)*(length*length + height*height)}" izz="${(base_mass/12)*(length*length + width*width)}" ixy="0" ixz="0" iyz="0" />
        </inertial>
    </link>

    <joint name="chassis_joint" type="fixed">
        <parent link="base_link" />
        <child link="chassis" />
        <origin xyz="0 0 0" rpy="0 0 0" />
    </joint>

    <joint name="base_to_back_left_wheel" type="continuous">
        <parent link="chassis" />
        <child link="back_left_wheel" />
        <origin xyz="0 ${wheel_width/2} ${wheel_radius}" rpy="-${pi/2} 0 0" />
        <axis xyz="0 0 1" />
    </joint>

    <xacro:wheel_link name="back_left_wheel" radius="${wheel_radius}" length="${wheel_length}" mass="${wheel_mass}" />

    <joint name="base_to_back_right_wheel" type="continuous">
        <parent link="chassis" />
        <child link="back_right_wheel" />
        <origin xyz="0 ${-wheel_width/2} ${wheel_radius}" rpy="${pi/2} 0 0" />
        <axis xyz="0 0 -1" />
    </joint>

    <xacro:wheel_link name="back_right_wheel" radius="${wheel_radius}" length="${wheel_length}" mass="${wheel_mass}" />

    <joint name="base_to_front_left_hinge" type="revolute">
        <parent link="chassis" />
        <child link="front_left_hinge" />
        <origin xyz="${wheelbase} ${hinge_d} ${wheel_radius}" />
        <axis xyz="0 0 1" />
        <limit lower="${-pi/4}" upper="${pi/4}" effort="10" velocity="50" />
    </joint>

    <link name="front_left_hinge">
        <inertial>
            <mass value="${hinge_mass}" />
            <inertia ixx="${hinge_mass*0.01}" iyy="${hinge_mass*0.01}" izz="${hinge_mass*0.01}" ixy="0" ixz="0" iyz="0" />
        </inertial>
    </link>

    <joint name="front_left_hinge_to_wheel" type="continuous">
        <parent link="front_left_hinge" />
        <child link="front_left_wheel" />
        <origin xyz="0 ${wheel_width/2 - hinge_d} 0" rpy="${-pi/2} 0 0" />
        <axis xyz="0 0 1" />
    </joint>

    <xacro:wheel_link name="front_left_wheel" radius="${wheel_radius}" length="${wheel_length}" mass="${wheel_mass}" />

    <joint name="base_to_front_right_hinge" type="revolute">
        <parent link="chassis" />
        <child link="front_right_hinge" />
        <origin xyz="${wheelbase} ${-hinge_d} ${wheel_radius}" />
        <axis xyz="0 0 1" />
        <limit lower="${-pi/4}" upper="${pi/4}" effort="10" velocity="50" />
    </joint>

    <link name="front_right_hinge">
        <inertial>
            <mass value="${hinge_mass}" />
            <inertia ixx="${hinge_mass*0.01}" iyy="${hinge_mass*0.01}" izz="${hinge_mass*0.01}" ixy="0" ixz="0" iyz="0" />
        </inertial>
    </link>

    <joint name="front_right_hinge_to_wheel" type="continuous">
        <parent link="front_right_hinge" />
        <child link="front_right_wheel" />
        <origin xyz="0 ${-wheel_width/2 + hinge_d} 0" rpy="${pi/2} 0 0" />
        <axis xyz="0 0 -1" />
    </joint>

    <xacro:wheel_link name="front_right_wheel" radius="${wheel_radius}" length="${wheel_length}" mass="${wheel_mass}" />

</robot>

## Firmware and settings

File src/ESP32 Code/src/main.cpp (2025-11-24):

#include <Arduino.h>
#include <cmath>

#include "OLED.h"
#include "battery.h"
#include "bno.h"
#include "io_pins.h"
#include "motors.h"
#include "parking_operations.h"

// --- Configuration ---
#define ENABLE_HW_TEST 0  // Set to 1 to enable hardware test mode (random movements)
#define COMM_SER Serial1  // Serial port for communication with Raspberry Pi

// --- IR Sensor Globals ---
bool IR_Enabled = false;
float IR_VAL_3 = 4096;
int IR_THRESH_3 = 20;
float IR_VAL_4 = 4096;
int IR_THRESH_4 = 20;

// --- Motor & Servo Globals ---
const float TPM = 1873.0;  // Ticks per meter (Encoder calibration)
Motors motors;
int cam_current = CAM_SERVO_CENTER_US;
bool cam_control = false; // Flag to enable/disable camera servo updates

// --- Movement State ---
float spdMult = 0.75;
int srlToSpd = 1000; // Max speed scaling factor
int spd = 0;
int str_angle = SERVO_CENTER_US;  // Current steering angle
long lastEncoderPos = 0;
long currentEncoderPos = 0;
float headingPrev = 0.0;
float Current_angle = 0.0;

// --- Odometry & Navigation ---
float posX = 0.0, posY = 0.0;
float sectionHeading = 0.0;
// Parking distances received from Pi (Left, Front-Left, Front, Front-Right, Right)
int dstL = 0, dstFL = 0, dstF = 0, dstFR = 0, dstR = 0;

// Parking Logic Parameters
float moveSideDist = 35.0; // Distance to move sideways for alignment
float parkFrontDist[] = {85, 150}; // Target distances for parking spots (Front/Back)
bool park_is_back = false; // True if parking in the second (further) spot
bool turning = false;
int turnCount = 0;

// --- System State ---
long LEDtmr = 0;
long srlTmr = 0;
long stopTmr = 0;
bool stop_bot = 0;
bool running = false;
String command = "none"; // Current high-level state/command

// --- Helper Functions ---

// Debug helper to track command transitions
void setCommand(const String &newCmd, const char *origin){
    if(command != newCmd){
        COMM_SER.print(">>CMD_CHANGE: ");
        COMM_SER.print(command);
        COMM_SER.print(" -> ");
        COMM_SER.print(newCmd);
        COMM_SER.print("  @ ");
        COMM_SER.println(origin);
    }
    command = newCmd;
}

float tomove = 0.0;
int key = 0; // Holds the command key (first byte of serial packet)

long lastOdomSent = 0;
#define odomSendInterval 50 // Send odometry every 50ms

float lerp(float a, float b, float t){
    return a + (b-a)*t;
}

/**
 * Serial Communication Handler.
 * Reads bytes from the Raspberry Pi and updates robot state.
 * Protocol: [Key Byte] -> [Value Byte]
 */
void srl() {
    // Send Odometry to Pi periodically
    if (running && millis() - lastOdomSent > odomSendInterval) {
        // Format: [x, y, theta] (Note: Coordinate system adjustments applied here)
        COMM_SER.printf("[%f,%f,%f]\n", -posY, posX, -heading);
        lastOdomSent = millis();
    }

    while (COMM_SER.available()) {
        int v = COMM_SER.read();
        
        // Reset LED timer on activity
        if(command == "none"){
            LEDtmr = millis();
        }

        // --- Single Byte Commands/Keys (0-49) ---
        if (v == 1) {
            setCommand("right45","srl:1");
        } else if (v == 2) {
            setCommand("left45","srl:2");
        } else if (v == 3) {
            setCommand("straight","srl:3");
        } else if (v == 4) {
            setCommand("passTurn","srl:4");
        } else if (v == 5) {
            setCommand("go","srl:5");
        } 
        // Parking Commands
        else if (v == 6) {
            setCommand("moveRight","srl:6"); // Park Right Spot
            park_is_back = false;
            motors.hardbreak_enabled(false);
        } else if (v == 8) {
            setCommand("moveLeft","srl:8");  // Park Left Spot
            park_is_back = true;
            motors.hardbreak_enabled(false);
        } 
        
        // System Commands
        else if (v == 30){
            bnoResetNormalize(); // Reset IMU
        }
        else if (v == 47){
            LEDtmr = millis(); // Keep-alive
        }
        else if (v == 49) {
            tone(BUZZER_PIN, BUZZ_MID, 250); // Camera Handshake OK
        }
        // Store Key for next byte
        else if (v < 50) {
            key = v;
        }

        // --- Two Byte Commands (Key stored, Value >= 50) ---
        if (key != 0 && v >= 50) {
            // Throttle (Key 15)
            if (key == 15) {
                spd = map(v, 50, 250, -srlToSpd, srlToSpd);
            }
            // Steering (Key 16)
            if (key == 16) {
                str_angle = map(v, 50, 250, SERVO_MIN_US, SERVO_MAX_US);
            }
            // Camera Servo (Key 17)
            if (key == 17) {
                int ang = constrain(v - 50, CAM_SERVO_ANGLE_MIN, CAM_SERVO_ANGLE_MAX);
                int t_us = map(ang, CAM_SERVO_ANGLE_MIN, CAM_SERVO_ANGLE_MAX, CAM_SERVO_MIN_US, CAM_SERVO_MAX_US);
                if(cam_control){
                    motors.setCamServoUs(t_us);
                }
                else{
                    motors.setCamServoUs(CAM_SERVO_CENTER_US);
                }
            }

            // Lidar distances from 5 directions (Keys 31-35)
            if(key == 31) dstL = v - 50;
            if(key == 32) dstFL = v - 50;
            if(key == 33) dstF = v - 50;
            if(key == 34) dstFR = v - 50;
            if(key == 35) dstR = v - 50;
            
            key = 0; // Reset key after processing value
        }
    }
}

/**
 * Odometry Calculation.
 * Updates global X, Y position based on encoder ticks and IMU heading.
 */
void odometry() {
    if(IR_Enabled){
        IR_VAL_3 = lerp(IR_VAL_3, analogRead(IR3_PIN), 0.1);
        IR_VAL_4 = lerp(IR_VAL_4, analogRead(IR4_PIN), 0.1);
    }
    currentEncoderPos = motors.getEncoderCount();
    float deltaEncoderPos = (currentEncoderPos - lastEncoderPos) / TPM;
    float ang = (heading + headingPrev) / 2; // Average heading during step
    headingPrev = heading;
    lastEncoderPos = currentEncoderPos;

    if (abs(deltaEncoderPos) > 0) {
        float deltaX = deltaEncoderPos * cos(ang * DEG_TO_RAD);
        float deltaY = deltaEncoderPos * sin(ang * DEG_TO_RAD);

        posX += deltaX;
        posY += deltaY;
    }
}

/**
 * FreeRTOS Task: Serial & Odometry Loop.
 * Runs on Core 1 to handle communication independently of motor control.
 */
void srlRead(void* pvParameters) {
    while (true) {
        odometry();
        srl();

        // Blink Status LED based on activity
        if (millis() - LEDtmr < 200) {
            digitalWrite(STATUS_LED, HIGH);
        } else {
            digitalWrite(STATUS_LED, LOW);
        }
        vTaskDelay(10 / portTICK_PERIOD_MS);
    }
}

void enableIR(){
    IR_Enabled = true;
    digitalWrite(IR_EN, HIGH);
}
void disableIR(){
    IR_Enabled = false;
    digitalWrite(IR_EN, LOW);
}

void startSerialReadTask() {
    xTaskCreatePinnedToCore(srlRead, "SerialTask", 4096, NULL, 10, NULL, 1);  // Core 1, high priority
}

// --- Setup ---
void setup() {
    // Initialize Sensors & Comms
    initBNO();
    startBNOCalcTask();
    initADC();

    Serial1.begin(115200, SERIAL_8N1, 19, 23); // To Pi
    Serial.begin(115200); // Debug
    enableIR();
    initOLED();
    startOLEDDisplayTask();
    displayText("Wait...");

    motors.begin();
    initIO();

    // Clear serial buffer
    while (COMM_SER.available() > 0) {
        COMM_SER.read();
    }

    startSerialReadTask();  // Start comms task
    motors.setServoUs(SERVO_CENTER_US);
    motors.setCamServoUs(CAM_SERVO_CENTER_US);
    
    // Calibrate IMU offset
    bnoCalcOffset(1500);
    
    displayText("All okay!");
    // Startup Beep
    tone(BUZZER_PIN, BUZZ_HIGH, 250);
    tone(BUZZER_PIN, BUZZ_MID, 250);
    noTone(BUZZER_PIN);

    // Handshake with Pi camera system
    COMM_SER.println(F("CONF_CAM"));

    // Wait for Start Button Press
    while (digitalRead(BUTTON_PIN) == HIGH) {
        vTaskDelay(50 / portTICK_PERIOD_MS);
    }
    disableIR();
    parkingSpeedHigh();
    
    // Wait for Button Release
    while (digitalRead(BUTTON_PIN) == LOW) {
        vTaskDelay(50 / portTICK_PERIOD_MS);
    }
    
    // Start Sequence
    bnoCalcOffset(200);    // Zero heading
    cam_control = true;
    tone(BUZZER_PIN, BUZZ_HIGH, 500);
    
    COMM_SER.println(F("Boot")); // Signal Pi to start
    displayText("");
    
    // Reset State
    motors.setServoUs(SERVO_CENTER_US);
    motors.setMotorSpeed(0);
    lastEncoderPos = motors.getEncoderCount();
    headingPrev = heading;
    posX = 0.0;
    posY = 0.0;

    sectionHeading = heading;
    startTime = millis();
    running = true;

    // Hardware Test Mode (Optional)
    #if ENABLE_HW_TEST
        randomSeed(esp_random());
        while (true) {
            motors.run(random(-255, 256));
            motors.setServoUs(random(SERVO_MIN_US, SERVO_MAX_US + 1));
            motors.setCamServoUs(random(CAM_SERVO_MIN_US, CAM_SERVO_MAX_US + 1));
            if (random(0, 1000) < 50) {
                tone(BUZZER_PIN, BUZZ_LOW, 500);
                digitalWrite(STATUS_LED, HIGH);
                delay(random(300, 800));
                digitalWrite(STATUS_LED, LOW);
            }
            vTaskDelay(random(300, 1500) / portTICK_PERIOD_MS);
        }
    #endif
}

/**
 * Complex Parking Maneuver.
 * Executes a series of turns to wiggle into the parking box.
 * @param dir: 1 for Left, -1 for Right
 */
void paark(int dir){
    cam_control = false;

    motors.setServoUs(SERVO_CENTER_US);
    vTaskDelay(50 / portTICK_PERIOD_MS);
    move_pos(0.15, 0.0); // Move forward slightly

    // Wiggle maneuver
    turn_angle_opp(25*dir);
    turn_angle(25*dir);
    turn_angle_opp(50*dir);
    turn_angle(65*dir);
    turn_angle_opp(75*dir);
    turn_angle(90*dir);
    turn_angle_opp(90*dir);
    motors.setMotorSpeed(0);
    motors.setServoUs(SERVO_CENTER_US);
}

void turn_div(int dir){
    turn_angle_opp(18*dir);
    turn_angle(36*dir);
    turn_angle_opp(54*dir);
    turn_angle(72*dir);
    turn_angle_opp(90*dir);
}

// --- Main Loop ---
void loop() {
    displayText(command);

    // --- Initialization Turns ---
    if (command == "right45") {
        turn_angle(45); // Actually turns 90 deg relative to start?
        setCommand("none","loop:right45");
        COMM_SER.println("Turned");
    }

    if (command == "left45") {
        turn_angle(-45);
        setCommand("none","loop:left45");
        COMM_SER.println("Turned");
    }

    // --- Parking Setup Moves ---
    if (command == "straight") {
        motors.setServoUs(SERVO_CENTER_US);
        move_pos(0.10);
        parkingSpeedLow();
        turn_angle(0); // Re-align to 0
        setCommand("none","loop:straight");
        COMM_SER.println("Done");
        posX = 0.0;
        posY = 0.0;
        motors.hardbreak_enabled(true);
    }
    if (command == "passTurn") {
        // Adjust heading if facing wrong way
        if (heading > 0) {
            turn_angle(135);
        } else {
            turn_angle(-135);
        }
        parkingSpeedLow();
        turn_angle(0);
        setCommand("none","loop:passTurn");
        COMM_SER.println("Done");
        posX = 0.0;
        posY = 0.0;
        motors.hardbreak_enabled(true);
    }

    // --- Main Driving Mode ---
    if (command == "go") {
        motors.setMotorSpeed(spd);
        motors.setServoUs(str_angle);
        vTaskDelay(10 / portTICK_PERIOD_MS);  // Yield
    }

    // --- Parking Sequence Start ---
    if(command == "moveRight"){
        // Align 45 degrees to approach parking lane
        turn_angle(0);
        turn_angle(45);
        motors.setServoUs(SERVO_CENTER_US);
        vTaskDelay(100 / portTICK_PERIOD_MS);
        
        // Calculate diagonal distance
        float tomove = dstFR - moveSideDist;
        tomove = tomove * 1.4142; // Hypotenuse
        
        tone(BUZZER_PIN, BUZZ_LOW, 200);
        move_pos(tomove/100);
        tone(BUZZER_PIN, BUZZ_HIGH, 200);
        
        setCommand("parkRight","loop:moveRight");
    }
    if(command == "moveLeft"){
        turn_angle(0);
        turn_angle(-45);
        motors.setServoUs(SERVO_CENTER_US);
        vTaskDelay(100 / portTICK_PERIOD_MS);
        
        float tomove = dstFL - moveSideDist;
        tomove = tomove * 1.4142;
        
        tone(BUZZER_PIN, BUZZ_LOW, 200);
        move_pos(tomove/100);
        tone(BUZZER_PIN, BUZZ_HIGH, 200);
        
        setCommand("parkLeft","loop:moveLeft");
    }

    // --- Parking Execution (Left Side) ---
    if(command == "parkLeft"){
        displayText("Parking Left");
        turn_angle(0); // Face forward
        vTaskDelay(500 / portTICK_PERIOD_MS);
        motors.setServoUs(SERVO_CENTER_US);

        // Move forward in steps to reach target distance
        parkingSpeedHigh();
        float toMove = dstF - parkFrontDist[park_is_back ? 1 : 0];
        move_pos(toMove/100, 0.0);
        vTaskDelay(500 / portTICK_PERIOD_MS);

        parkingSpeedLow();
        toMove = dstF - parkFrontDist[park_is_back ? 1 : 0];
        move_pos(toMove/100, 0.0);
        vTaskDelay(500 / portTICK_PERIOD_MS);

        toMove = dstF - parkFrontDist[park_is_back ? 1 : 0];
        move_pos(toMove/100, 0.0);

        displayText("Initializing Parking");

        turn_angle_opp(90);
        turn_angle_opp(90);
        move_pos(-0.27, 90.0);

        vTaskDelay(100 / portTICK_PERIOD_MS);
        // Decide final wiggle direction based on side clearance
        if(dstL > dstR){
            displayText("park_fin_R");
            setCommand("park_fin_R","loop:parkLeft");
        } else {
            displayText("park_fin_L");
            setCommand("park_fin_L","loop:parkLeft");
        }
    }

    // --- Parking Execution (Right Side) ---
    if(command == "parkRight"){
        displayText("Parking Right");
        turn_angle(0);
        vTaskDelay(500 / portTICK_PERIOD_MS);
        motors.setServoUs(SERVO_CENTER_US);

        COMM_SER.println(">>Front Dist: " + String(dstF));
        float toMove = dstF - parkFrontDist[park_is_back ? 1 : 0];
        COMM_SER.println(">>To Move: " + String(toMove));
        move_pos(toMove/100, 0.0);
        vTaskDelay(500 / portTICK_PERIOD_MS);

        toMove = dstF - parkFrontDist[park_is_back ? 1 : 0];
        move_pos(toMove/100, 0.0);
        vTaskDelay(500 / portTICK_PERIOD_MS);

        toMove = dstF - parkFrontDist[park_is_back ? 1 : 0];
        move_pos(toMove/100, 0.0);
        displayText("Initializing Parking");

        turn_angle_opp(-90);
        turn_angle_opp(-90);
        move_pos(-0.27, -90.0);

        vTaskDelay(100 / portTICK_PERIOD_MS);
        if(dstL > dstR){
            displayText("park_fin_R");
            setCommand("park_fin_R","loop:parkRight");
        } else {
            displayText("park_fin_L");
            setCommand("park_fin_L","loop:parkRight");
        }
    }

    // --- Final Parking Wiggle ---
    if(command == "park_fin_R"){
        bnoCalcOffset(500);
        COMM_SER.println(">>Parking Right");
        paark(-1);
        COMM_SER.println("Parked");
        command = "none";
    }
    if(command == "park_fin_L"){
        bnoCalcOffset(500);
        COMM_SER.println(">>Parking Left");
        paark(1);
        COMM_SER.println("Parked");
        command = "none";
    }

    // --- Idle State ---
    if (command == "none") {
        motors.setMotorSpeed(0);
        motors.setServoUs(SERVO_CENTER_US);
    }
}

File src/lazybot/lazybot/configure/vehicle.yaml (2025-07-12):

length: 20
width: 10
height: 15

sensors:
    - type: "sonar"
      position: [-5, 10]
      angle: -75
    - type: "sonar"
      position: [0, 10]
      angle: 0
    - type: "sonar"
      position: [5, 10]
      angle: 75
      
    - type: "proximity"
      position: [-5, 10]
      angle: -45
    - type: "proximity"
      position: [5, 10]
      angle: 45
    - type: "proximity"
      position: [-5, -10]
      angle: -135
    - type: "proximity"
      position: [5, -10]
      angle: 135

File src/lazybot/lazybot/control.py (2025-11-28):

import rclpy
from threading import Thread
from rclpy.node import Node
from sensor_msgs.msg import LaserScan
from geometry_msgs.msg import Vector3

from std_msgs.msg import Float32, Float32MultiArray, String, Int8MultiArray, Int8
from lazy_interface.msg import BotDebugInfo, LidarTowerInfo
from math import pi, radians, degrees, sin, cos
import time

from lazybot.helper.util import LidarHandler, clamp, remap, lerp, norm_ang

class ControlNode(Node):
    """
    Main Control Node for LazyBot.
    Handles sensor fusion (LiDAR, Odometry, Camera), path planning (Disparity Extender),
    obstacle avoidance, and motor control.
    """
    def __init__(self):
    
        super().__init__('control')

        # --- Parameters ---
        self.declare_parameter('IS_SIM', False)
        self.IS_SIM = self.get_parameter('IS_SIM').get_parameter_value().bool_value

        # --- Publishers & Subscribers ---
        
        # Command interface (Start/Stop/Direction)
        self.cmd_sub = self.create_subscription(String, '/cmd', self.cmd_callback, 10)
        self.cmd_pub = self.create_publisher(String, '/cmd', 10)
        
        # Sensor inputs
        self.sensor_sub = self.create_subscription(Int8MultiArray, '/lazybot/sensors', self.sensor_callback, 10)
        self.lidar_sub = self.create_subscription(LaserScan, '/scan', self.lidar_callback, 1)
        self.obj_sub = self.create_subscription(String, '/closest_obj', self.obj_callback, 1) # From Camera
        self.pos_sub = self.create_subscription(Vector3, '/lazypos', self.pos_callback, 10)   # From Odometry

        # Data outputs
        self.objPub = self.create_publisher(Float32MultiArray, '/obj_data', 1)
        
        # Actuator outputs
        self.throttle_pub = self.create_publisher(Float32, '/throttle', 1)
        self.steer_pub = self.create_publisher(Float32, '/steer', 1)
        self.cam_pub = self.create_publisher(Int8, '/cam_servo', 1) # Servo to point camera at towers

        # Debugging
        self.pubDebug = self.create_publisher(BotDebugInfo, '/lazybot/debug', 10)
        
        # --- Timers ---
        self.create_timer(0.025, self.odom_loop)    # 40Hz: Position & Lap Logic
        self.create_timer(0.025, self.control_loop) # 40Hz: Motor Command Publishing

        # --- State Variables ---
        self.IS_OPEN = False # False = Obstacle Challenge, True = Open Challenge
        self.dir = 1 # 1 = CCW (Counter-Clockwise), -1 = CW (Clockwise)
        
        self.lidar = LidarHandler() # Helper class to manage LiDAR arrays

        # --- Navigation Parameters ---
        
        # Speed Boosting (Go fast on straights)
        self.speedBoost = 1.0
        self.boostMax = 1.35 #1.25
        self.boostAngleThresh = 7.5 # Only boost if steering angle is within +/- 7.5 deg
        self.boostDistThresh = 1.10 # Only boost if clear path > 1.1m

        # Speed Limits
        self.maxSpeed : float = 0.60
        self.speedCap : float = 0.40
        self.targetCap : float = 0.40
        self.speedCapRng = [0.30, 0.45] # [Corner Speed, Straight Speed]
        self.speed : float = 0.0
        
        # Steering Parameters
        self.strAngle : float = 0.0
        self.strRange = 1.0 # Max steering value (normalized -1 to 1)
        self.str_ang_thresh = 60.0 # Max physical steering angle in degrees
        self.strSpd = 0.65 # Steering smoothing factor
        
        # LiDAR Processing
        self.prec = 81 # Precision window for marching algorithm
        self.skip1 = 2 # Skip factor for initial scan
        self.skip2 = 1 # Skip factor for fine checks

        # Safety
        self.dangerDist = 0.22 # Emergency avoidance distance
        self.dangerAng = [25.0, 90.0] # Angles to check for side collisions

        # Disparity Extender / Gap Follower Params
        self.new_lidar_val = False
        self.castRange = [0.13, 0.16] # Dynamic robot width (expands with speed)
        self.castR = 0.25 # Current cast radius
        self.lookRng = radians(80.0) # Field of view for path planning
        self.lookRngS = radians(130.0)
        self.targetAng = 0.0
        self.targetD = 0.0
        
        # --- Background Thread ---
        # Runs heavy LiDAR calculations separately from ROS callbacks
        self.calc_thr = Thread(target=self.calc_lidar)
        self.calc_thr.daemon = True
        self.calc_thr.start()

        # --- Odometry & Lap Counting ---
        self.pos = Vector3()
        self.sectionAngle = 0.0
        self.gotWallD = False
        self.reached = True
        self.lapCount = 0
        self.targetLap = 2
        self.running = False
        self.endOffset = [-0.5, 1.5] # Y-coordinates for Start/Finish area
        # Coordinates of track corners for special handling
        self.cornerPOS = [(0.0, 1.0), (0.0, -1.0), (2.0, 1.0), (2.0, -1.0), (-2.0, 1.0), (-2.0, -1.0)]

        self.objs = [] # Detected towers
        self.cont_stack = [] # Stack for edge detection
        
        self.closest = "N" # Closest object color: "R"ed, "G"reen, "N"one

        self.get_logger().info('Control node has been started.')
        self.lastTime = time.time()

    
    def sensor_callback(self, msg: Int8MultiArray):
        """Handles hardware limit switches or line sensors."""
        if len(msg.data) < 4:
            self.get_logger().warn("Received sensor data with insufficient length.")
            return
        
        # Hard steering override if sensors trigger
        if msg.data[0] == 1:
            self.strAngle = -self.strRange
        if msg.data[1] == 1:
            self.strAngle = self.strRange
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

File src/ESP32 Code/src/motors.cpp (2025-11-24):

#include "motors.h"

#include <driver/mcpwm.h>
#include <freertos/FreeRTOS.h>
#include <freertos/task.h>
#include <math.h>

extern float spdMult;
// Initialize static member
Motors* Motors::instance = nullptr;

void IRAM_ATTR Motors::encoderISR() {
    static unsigned long lastInterruptTime = 0;
    unsigned long interruptTime = micros();
    if (interruptTime - lastInterruptTime > 10)  // debounce 10us
    {
        if (instance) {
            if (digitalRead(ENCODER_B) == HIGH) {
                instance->encoderCount++;
            } else {
                instance->encoderCount--;
            }
            // Position control removed; keep only encoder count
        }
    }
    lastInterruptTime = interruptTime;
}

void Motors::control_enabled(bool en){
    do_control = en;
}

void Motors::hardbreak_enabled(bool en){
    hardbreak_en = en;
}

// FreeRTOS task for PID speed and position control
void Motors::speedControlTask(void* pvParameters) {
    // Simple PI speed controller using encoder feedback (mm/s)
    // Runs periodically with minimal blocking via vTaskDelayUntil.

    // Access global ticks-per-meter defined in main.cpp
    extern const float TPM;  // ticks per meter

    // Controller parameters (tuned conservatively)
    const TickType_t periodTicks = pdMS_TO_TICKS(80);  // 12.5 Hz control
    const float dt = 0.080f;                           // 80 ms
    const float kp = 0.04f;                           // proportional gain
    const float ki = 0.35f;                            // integral gain (per second)
    const int maxPWM = 255;
    const int minPWM = 18;        // overcome static friction
    const int slewPerCycle = 200;  // limit change per cycle 
    const float FF_GAIN = 0.0f;   // feedforward: gives a beginning push, set to 0.0 to disable, (0.10-0.40) might help with low speeds  but too much can make car jump

    TickType_t lastWake = xTaskGetTickCount();
    Motors* self = static_cast<Motors*>(pvParameters);
    long lastTicks = self->encoderCount;
    float integrator = 0.0f;
    int cmdPWM = 0;  // command in -255..255

    while (true) {
        if(!self->do_control){
            vTaskDelay(periodTicks);
            continue;
        }
        // Measure actual speed (mm/s)
        long ticksNow = self->encoderCount;
        long dTicks = ticksNow - lastTicks;
        lastTicks = ticksNow;

        float delta_m = (float)dTicks / TPM;        // meters in dt
        float meas_mms = (delta_m * 1000.0f) / dt;  // mm/s

        // Target speed in mm/s (no position control)
        float target_mms = self->target_speed_mms;

        // Basic PI control
        float err = target_mms - meas_mms;
        integrator += err * dt;  // integrate error (mm)
        // Anti-windup clamp
        if (integrator > 5000.0f) integrator = 5000.0f;
        if (integrator < -5000.0f) integrator = -5000.0f;

        // PI correction (integrator in mm*s)
        float piTerm = kp * err + ki * integrator;
        // Feedforward term based on desired speed
        int ff = (int)lroundf(FF_GAIN * target_mms);  // signed
        // Desired PWM = feedforward + PI correction
        int desiredPWM = ff + (int)lroundf(piTerm);

        // Near-zero target -> stop cleanly
        if (fabsf(target_mms) < 3.0f) {
            desiredPWM = 0;
            integrator = 0;
        }

        // Apply deadband when commanding motion
        if (desiredPWM != 0) {
            if (desiredPWM > 0 && desiredPWM < minPWM) desiredPWM = minPWM;
            if (desiredPWM < 0 && desiredPWM > -minPWM) desiredPWM = -minPWM;
        }

        // Slew-rate limit
        int deltaCmd = desiredPWM - cmdPWM;
        if (deltaCmd > slewPerCycle) deltaCmd = slewPerCycle;
        if (deltaCmd < -slewPerCycle) deltaCmd = -slewPerCycle;
        cmdPWM += deltaCmd;

        // Clamp to valid range
        if (cmdPWM > maxPWM) cmdPWM = maxPWM;
        if (cmdPWM < -maxPWM) cmdPWM = -maxPWM;

        // Drive motor
        self->run(cmdPWM);

        // Keep timing stable without blocking other tasks
        vTaskDelayUntil(&lastWake, periodTicks);
    }
}

void Motors::begin() {
    instance = this;       // Set the static instance pointer
    encoderCount = 0;      // Initialize encoder count
    target_speed_mms = 0;  // Initialize target speed
    do_control = true;
    hardbreak_en = false;
    // Position control removed

    // Configure MCPWM for steering servo (Timer 0, Operator A)
    mcpwm_gpio_init(MCPWM_UNIT_0, MCPWM0A, SERVO_PIN);
    mcpwm_config_t pwm_config = {
        .frequency = 50,                   // 50 Hz for servo
        .cmpr_a = 0,                       // Initial duty cycle for operator A
        .cmpr_b = 0,                       // Initial duty cycle for operator B (not used)
        .duty_mode = MCPWM_DUTY_MODE_0,    // Duty cycle mode
        .counter_mode = MCPWM_UP_COUNTER,  // Counter mode
    };
    mcpwm_init(MCPWM_UNIT_0, MCPWM_TIMER_0, &pwm_config);

    // Configure MCPWM for camera servo (Timer 1, Operator A)
    mcpwm_gpio_init(MCPWM_UNIT_0, MCPWM1A, CAM_SERVO_PIN);
    mcpwm_config_t cam_pwm_config = {
        .frequency = 50,                   // 50 Hz for servo
        .cmpr_a = 0,                       // Initial duty cycle for operator A
        .cmpr_b = 0,                       // Initial duty cycle for operator B (not used)
        .duty_mode = MCPWM_DUTY_MODE_0,    // Duty cycle mode
        .counter_mode = MCPWM_UP_COUNTER,  // Counter mode
    };
    mcpwm_init(MCPWM_UNIT_0, MCPWM_TIMER_1, &cam_pwm_config);

    // Configure motor pins
    pinMode(MOTOR_IN1, OUTPUT);
    pinMode(MOTOR_IN2, OUTPUT);
    pinMode(MOTOR_PWM, OUTPUT);
    pinMode(MOTOR_ENB, OUTPUT);
    pinMode(ENCODER_A, INPUT);
    pinMode(ENCODER_B, INPUT);
    digitalWrite(MOTOR_ENB, HIGH);  // Enable motor driver

    // Disaled ledcSetup/ledcAttachPin/ledcWrite
    // Configure motor PWM for 18kHz
    // ledcSetup(MOTOR_PWM_CHANNEL, MOTOR_PWM_FREQ, 8);  // Channel 0, 18kHz, 8-bit resolution
    // ledcAttachPin(MOTOR_PWM, MOTOR_PWM_CHANNEL);      // Attach PWM pin to channel 0
    attachInterrupt(digitalPinToInterrupt(ENCODER_A), encoderISR, RISING);

    // Add MCPWM for motor
    mcpwm_gpio_init(MCPWM_UNIT_0, MCPWM2A, MOTOR_PWM);  // Use Timer 2
    mcpwm_config_t motor_pwm = {
        .frequency = 18000,  // 18kHz
        .cmpr_a = 0,
        .duty_mode = MCPWM_DUTY_MODE_0,
        .counter_mode = MCPWM_UP_COUNTER,
    };
    mcpwm_init(MCPWM_UNIT_0, MCPWM_TIMER_2, &motor_pwm);

    // Create speed control task pinned to core 0
    xTaskCreatePinnedToCore(
        [](void* arg) { static_cast<Motors*>(arg)->speedControlTask(arg); },
        "SpeedControlTask",
        4096,
        this,
        1,
        nullptr,
        0);
}

void Motors::setServoUs(uint32_t pulse_width_us) {
    pulse_width_us = constrain(pulse_width_us, SERVO_MIN_US, SERVO_MAX_US);
    mcpwm_set_duty_in_us(MCPWM_UNIT_0, MCPWM_TIMER_0, MCPWM_OPR_A, pulse_width_us);
}
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

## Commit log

2025-07-20 Added newest ESP32 code with BNO055
2025-07-25 Adding a gazebo simulation for the WRO 2025 track.
    [camera.xacro, control.xacro, controller_config.yaml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]
2025-07-26 Object detection with lidar
    [lazyBotCore.xacro, lidar.xacro]
2025-07-26 camera viewer
2025-07-27 Object avoidance (One sided)
    [control.xacro, controller_config.yaml]
2025-07-30 color calibration code
2025-08-01 Simulating object round
    [camera.xacro]
2025-08-04 modified: src/lazysim/description/control.xacro modified: src/lazysim/launch/gazebo.lazyBot.launch.py modified: src/lazysim/launch/rviz_lazySim.launch.py modified: src/lazysim/lazysim/lazybridge.py
    [control.xacro]
2025-08-05 Odom Calculation
    [IMU.xacro, lazyBot.xacro, lazyBotCore.xacro]
2025-08-05 Changed track creator parameters to yaml fixed bugs in the logic of lap counting
    [IMU.xacro, lazyBot.xacro, lidar.xacro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]
2025-08-07 Added odometry to rviz
    [lazyBotCore.xacro]
2025-08-08 Custom interface for LazyBot Separated debug node from control node Added odometry and transform broadcasting
2025-08-09 resource folder added
    [proximity.xacro]
2025-08-19 Bug fixes
    [wall_template.sdf]
2025-08-25 modified: src/lazybot/lazybot/control.py modified: src/lazysim/config/lazySim.rviz modified: src/lazysim/config/track.yaml
2025-09-22 Fixed IMU issue
2025-09-22 Algorithm: Odometry and Movement Control
2025-09-24 camera issue
2025-09-24 mermaid flowcharts
    Added flowcharts for control loops and obstacle detection methods.
2025-09-24 parking calibration test
2025-09-24 Updated README.md
    Fixed power source description
2025-09-24 Update README.md
    Fixed flowchart and a few other things
2025-09-24 camera servo
2025-09-24 servo cam
2025-09-25 modified: src/ESP32 Code/src/main.cpp
2025-10-04 correction: servo model
2025-10-31 optimizes flowchart
2025-11-15 Update power flowchart in README
2025-11-16 Updated code for PCB V2
2025-11-16 Lidar direction flip fix
2025-11-16 Updated pins again since last pins had issues
    [battery.cpp, io_pins.h, main.cpp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]
2025-11-16 remove LEDC, add MCPWM, bnoCalcTask
2025-11-18 modified: src/ESP32 Code/src/main.cpp modified: src/ESP32 Code/src/motors.cpp modified: src/ESP32 Code/src/parking_operations.cpp
2025-11-20 fingers crossed!
2025-11-22 3d model files upload
    [CarTop Cover-.stl, Front wheel cover- x2.stl, PS-1171mg Servo Mount.stl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]
2025-11-23 simulation camera update
    [camera.xacro, control.xacro, controller_config.yaml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]
2025-11-23 button update
2025-11-23 Failed attempt to make the robot faster
    [control.py, debug.py, parking.py]
2025-11-23 Enhance README with images and formatting update
    Updated the README to include images for each stage of the robot's structure and improved formatting.
2025-11-24 pcb image updata
2025-11-24 Correct servo movement speed in README
2025-11-24 power system updated (somehow it was reverted back before)
2025-11-26 open round fixed self centering code inturripting turns
    [open_control.py]
2025-11-27 object detection lidar fix
    [control.py, debug.py]
2025-11-27 fixed only checking for green fixed object detection slope
    [control.py]
